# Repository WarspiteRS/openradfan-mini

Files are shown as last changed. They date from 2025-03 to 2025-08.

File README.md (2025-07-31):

# OpenRadFan
An ESPHome-driven smart controller for 12V PWM fans.

Classical radiators (K2/K3) typically require relatively high flow temperatures to heat up a room. Using forced convection can significally enhance their efficiency, especially at low flow temperatures. While there are a number of commercial solutions available, these did not need my needs. They are either too loud while running or switching on/off using a relays, don't properly switch at low flow temperatures, are too expensive or simply not powerful enough. Hence, I set out to build my own solution using standard 120/140mm PWM-capable PC fans. High-end fans run at low speeds (<500 RPM) are essentially inaudible and provide a definite boost to the room temperature. Being able to smartly control the fan speed and integrate them into Home Assistant - while not a must - is definitely very nice to have if you want to control fan speed based on time of day, current room temperature or room occupancy. The fans can even be used as a kind of thermostat to modulate room temperature without restricting flow to the radiators, which is especially crucial when using a heat pump that perform best with an open loop circulation and no TRVs.

Using these devices throughout our house, we can run out heat pump at flow temperatures typically reserved for good underfloor heating setups (Vaillant heat curve at 0.25 - 30°C flow temperature at 0°C, 35°C flow temperature at -10°C).

<p align="center">
  
</p>

## Features
### Hardware
- M5Stack Atom Lite / Atom Lite S3 pluggable µC with usable Grove port for arbitrary I2C device support
- 8 fan connectors in 2x4 rows *[OpenRadFan-mini only has 2 fan connectors in 2x1 rows]*
- Each row can be individually PWM controlled (this is not enabled by default)
- RPM measurement for the first fan in each row *[OpenRadFan-mini only has one fan in each row]*
- Global on/off switch for fans that don't support zero output at zero PWM
- Plug-in connector for two DS18B20-compatible temperature sensors *[OpenRadFan-mini only has one temperature sensor]*
- Power supply: 12V barrel jack (2.1/2.5 mm), center positive
- Reverse voltage & transient overvoltage protection, 2.5 A resettable fuse
### Software
- Fully ESPHome compatible
- Controllable via Home Assistant or through any browser via stand-alone webserver
- Automatic fan curve driven speed control
- Setup & Connection to local WiFi via improv WiFi Hotspot on first boot

## Set-up instructions
**Don't connect to USB when the Atom lite is plugged into the PCB - there is no mechanism to block voltages between the included buck converter and the computer.**
1. Compile & flash ESPHome firmware on the Atom Lite using USB. Skip this step if you have a pre-flashed controller. The ESPHome directory on GitHub contains the yaml as well as factory & ota images so you can directly flash this without a local ESPHome compiler set up.
2. Connect DS18B20 to the push-in terminal block. The wire designations are marked on the PCB and are (from left to right): +3.3V, Data, GND. It's easiest to insert them all at the same time. Hold the wires in one hand in the correct order and insert them into the terminal. Then push all orange levers down at the same time and push the wires down as far as possible. The levers should almost return to the initial position and not be stuck halfway down. If you want to use more than one sensor, you need to manually edit the ESPHome yaml and include the individual IDs of the DS18B20s.
<p align="center">
  
</p>
4. Plug in the Atom Lite controller module and fans.
5. Lastly, plug in the barrel plug to power the device
6. On first boot, the device will present a hotspot named "openradfan-xxxxxx", with xxxxxx being the last characters of the Atom Lite's MAC address. You can connect to it in order to enter your WiFi credentials. The passwort for the hotspot is "OpenRadFan". If you get a warning that the hotspot does not provide an internet connection, click "Yes" when asked to connect anyways. Then, point your browser to http://192.168.4.1 to open the config page. Tap/click on your home WiFi and enter the password. Note down the hostname shown after "Wifi Networks:" (here "openradfan-f9465c"), this is also the hostname you can use to connect to the web interface after it has connected to your Wifi via http://openradfan-xxxxxx. It might be required to power cycle if you don't see the device appearing in your network.
<p align="center">
  
  
  
</p>
8. Home Assistant should automatically detect the device under Settings --> Devices & Services

<p align="center">
  
</p>
9. You can adopt it in your local ESPHome environment. The full yaml code will be fethed from GitHub when you do so, so you can adapt the config if needed.
10. The web interface gives you full control over all aspects of the device. Over-the-air (OTA) updates can also be uploaded and flashed to the device.
<p align="center">
  
</p>

## Fan curve control
You can set 5 temperature points and associated fan speeds to build a temperature-dependent fan speed response. The speed between the points is interpolated linearly. The temperatures have to increase from 1 to 5; this is also enforced by internal logic. Temperatures above/below the highest/lowest setpoint keep the speed of this setpoint. Set "Auto Fan Curve Control" to on in order to use this feature.

In the below example, the fans are off below 20°C, increase between 0 and 29% speed in the range between 20 and 21°C, then increase up to 100% at 25°C. Above that, speed decreases to 28% at 30°C and the fans are off again at 35°C.

When fan speed is set to zero, the internal high-level switch also cuts all power to the fans. Some fans (e.g. Arctic PXX PWM) turn off with a zero PWM signal and wouldn't need this functionality, however many other fans cannot be turned off via PWM alone.
<p align="center">
  
</p>

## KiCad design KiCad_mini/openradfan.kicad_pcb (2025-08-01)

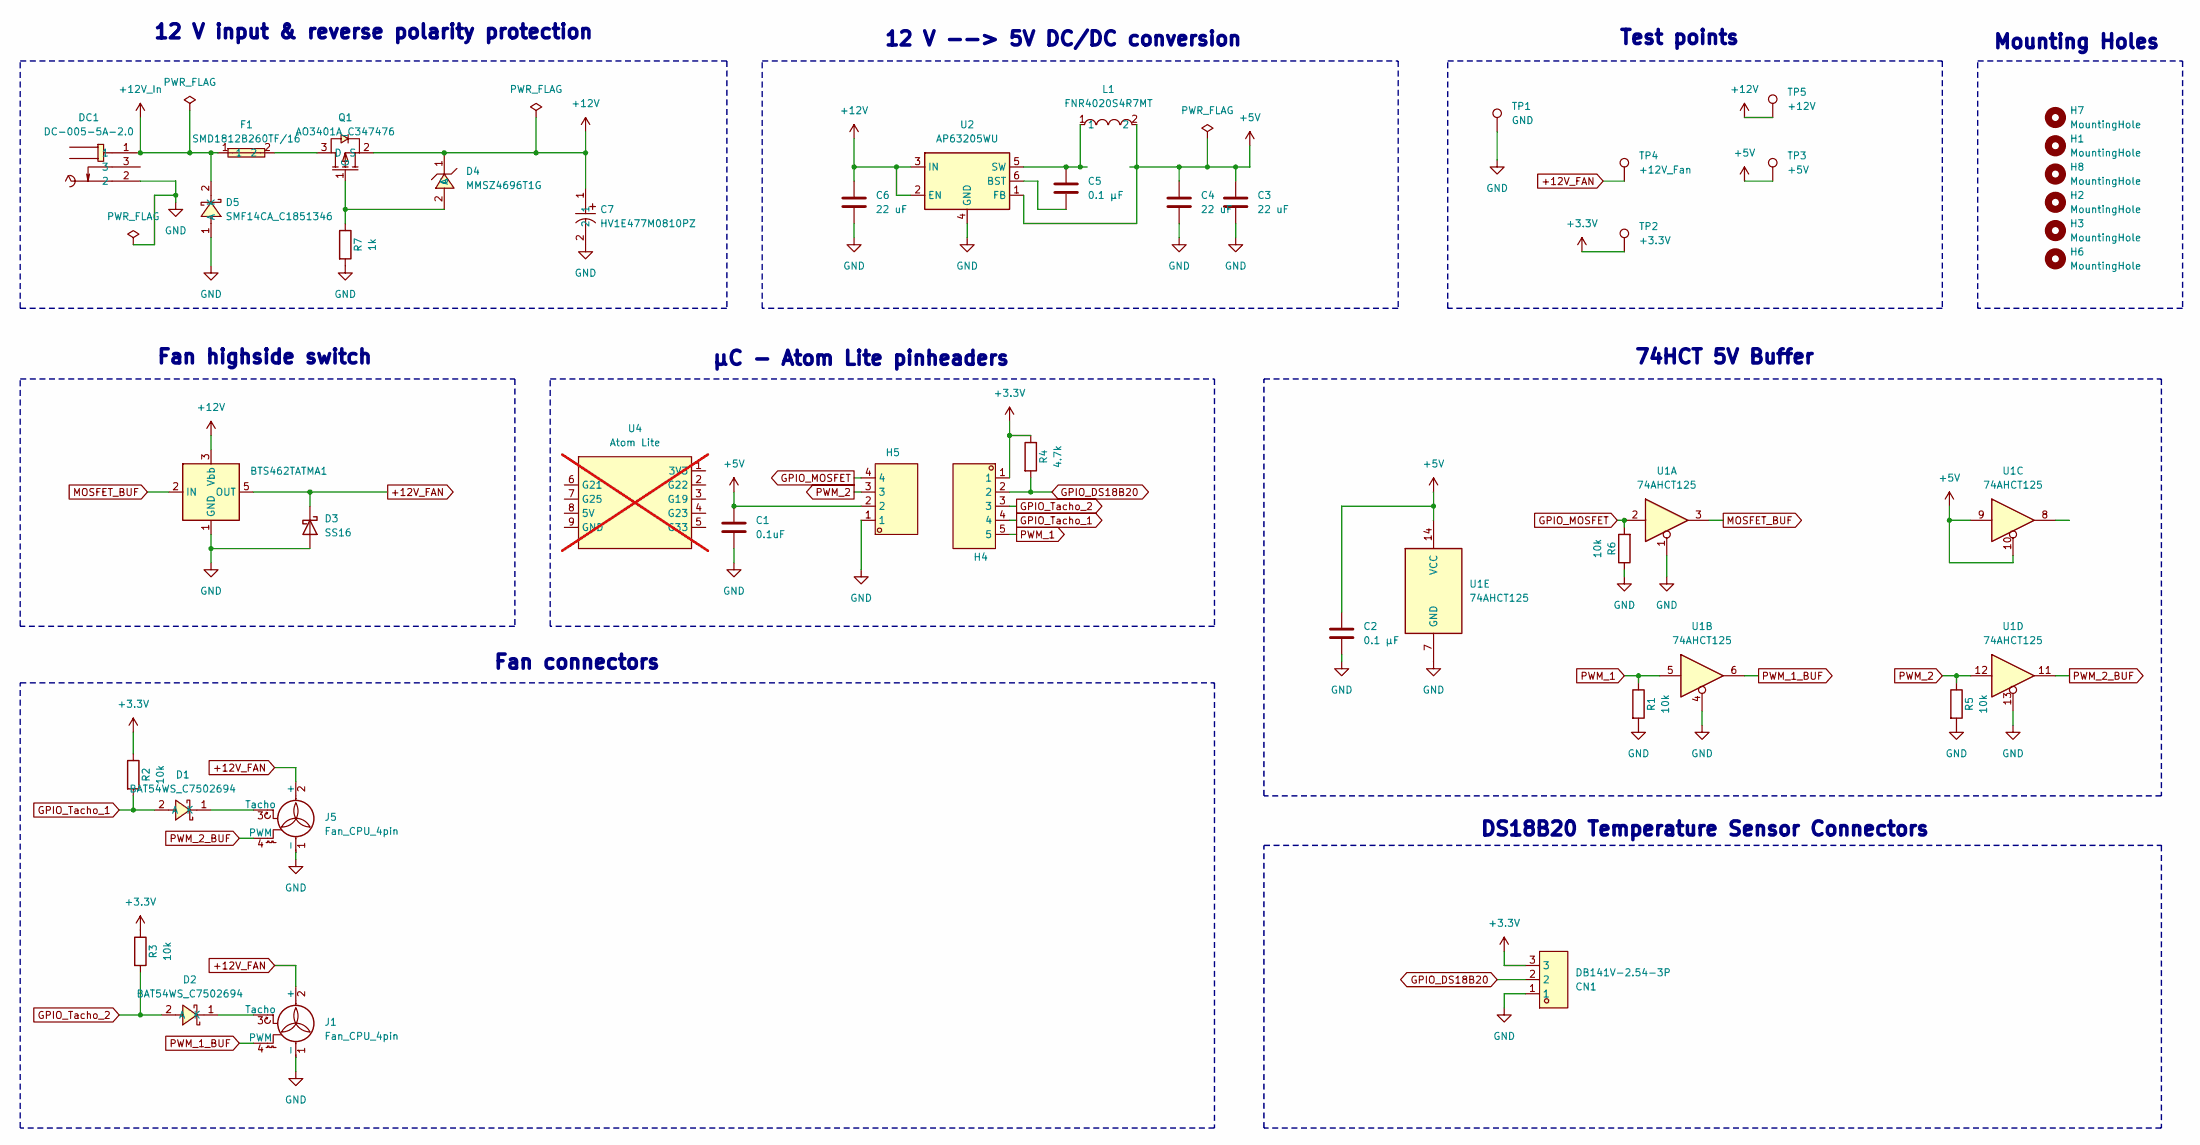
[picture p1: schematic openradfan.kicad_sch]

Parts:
C1: 0.1uF; C_0805_2012Metric_Pad1.18x1.45mm_HandSolder; LCSC Part # C28233
C2: 0.1 µF; C_0805_2012Metric_Pad1.18x1.45mm_HandSolder; LCSC Part # C28233
C3, C4, C6: 22 uF; C_1210_3225Metric; LCSC Part # C309062
C5: 0.1 µF; C_0402_1005Metric; LCSC Part # C1525
C7: HV1E477M0810PZ; CAP-SMD_BD8.0-L8.3-W8.3-LS9.3-FD-2; LCSC Part C5246546
CN1: DB141V-2.54-3P; CONN-TH_3P-P2.54_DIBO_DB141V-2.54-3P; LCSC Part C2898745
D1, D2: BAT54WS_C7502694; SOD-323_L1.7-W1.3-LS2.6-RD-1; LCSC Part C7502694
D3: SS16; D_SMA; LCSC Part # C2481
D4: MMSZ4696T1G; SOD-123_L2.7-W1.6-LS3.7-RD-1; LCSC Part C462868
D5: SMF14CA_C1851346; SOD-123_L2.8-W1.8-LS3.7-BI; LCSC Part C41411783
DC1: DC-005-5A-2.0; DC-IN-TH_DC-005-5A-2.0; LCSC Part C381116
F1: SMD1812B260TF/16; F1812; LCSC Part C269148
H1, H2, H7, H8: MountingHole; MountingHole_3.2mm_M3_DIN965
H3, H6: MountingHole; MountingHole_2.2mm_M2_DIN965
H4: 210S-1*5P L=11.6MMGold-plated black; HDR-TH_5P-P2.54-V-M; LCSC Part C124379
H5: Header-Male-2.54_1x4; HDR-TH_4P-P2.54-V-M; LCSC Part C124378
J1, J5: Fan_CPU_4pin; FanPinHeader_1x04_P2.54mm_Vertical; MPN 0470531000; LCSC Part # C240840
L1: FNR4020S4R7MT; IND-SMD_L4.0-W4.0_FNR40XXS; LCSC Part C167828
Q1: AO3401A_C347476; SOT-23_L2.9-W1.3-P1.90-LS2.4-BR; LCSC Part C347476
R1, R2, R3, R5, R6: 10k; R_0805_2012Metric_Pad1.20x1.40mm_HandSolder; LCSC Part # C17414
R4: 4.7k; R_0805_2012Metric_Pad1.20x1.40mm_HandSolder; LCSC Part # C17673
R7: 1k; R_0603_1608Metric; LCSC Part # C21190
TP1: GND; TestPoint_Keystone_5000-5004_Miniature
TP2: +3.3V; TestPoint_Keystone_5000-5004_Miniature
TP3: +5V; TestPoint_Keystone_5000-5004_Miniature
TP4: +12V_Fan; TestPoint_Keystone_5000-5004_Miniature
TP5: +12V; TestPoint_Keystone_5000-5004_Miniature
U1: 74AHCT125; SOIC-14_3.9x8.7mm_P1.27mm; MPN SN74AHCT125N; LCSC Part # C352957
U2: AP63205WU; TSOT-23-6; LCSC Part # C2071056
U3: BTS462TATMA1; TO-252-4; LCSC Part # C3232325
U4: Atom Lite; not fitted

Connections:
+3.3V: CN1.3, H4.1, R2.1, R3.1, R4.1, TP2.1
+5V: C1.1, C2.1, C3.1, C4.1, H5.2, L1.2, TP3.1, U1.9, U1.10, U1.14 (VCC), U2.1 (FB)
+12V: C6.1, C7.1, D4.1 (C), Q1.2 (S), TP5.1, U2.2 (EN), U2.3 (IN), U3.3 (Vbb)
+12V_FAN: D3.1 (K), J1.2 (+), J5.2 (+), TP4.1, U3.5 (OUT)
+12V_In: D5.2 (K), DC1.1, F1.1
GND: C1.2, C2.2, C3.2, C4.2, C6.2, C7.2, CN1.1, D3.2 (A), D5.1 (A), DC1.2, H5.1, J1.1 (-), J5.1 (-), R1.2, R5.2, R6.1, R7.2, TP1.1, U1.1, U1.4, U1.7 (GND), U1.13, U2.4 (GND), U3.1 (GND)
GPIO_DS18B20: CN1.2, H4.2, R4.2
GPIO_MOSFET: H5.4, R6.2, U1.2
GPIO_Tacho_1: D1.2 (A), H4.4, R2.2
GPIO_Tacho_2: D2.2 (A), H4.3, R3.2
MOSFET_BUF: U1.3, U3.2 (IN)
unnamed: D1.1 (K), J5.3 (Tacho)
unnamed: D2.1 (K), J1.3 (Tacho)
unnamed: D4.2 (A), Q1.1 (G), R7.1
unnamed: F1.2, Q1.3 (D)
unnamed: C5.2, U2.6 (BST)
unnamed: C5.1, L1.1, U2.5 (SW)
PWM_1: H4.5, R1.1, U1.5
PWM_1_BUF: J1.4 (PWM), U1.6
PWM_2: H5.3, R5.1, U1.12
PWM_2_BUF: J5.4 (PWM), U1.11

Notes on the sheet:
12 V input & reverse polarity protection
12 V --> 5V DC/DC conversion
µC - Atom Lite pinheaders
Fan connectors
Mounting Holes
74HCT 5V Buffer
Test points
Fan highside switch
DS18B20 Temperature Sensor Connectors

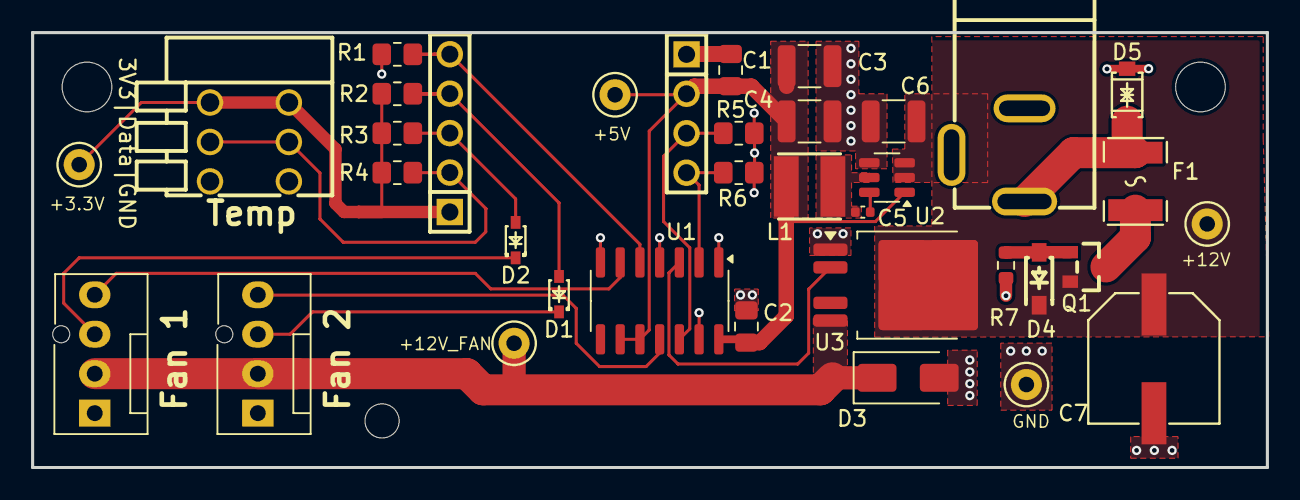
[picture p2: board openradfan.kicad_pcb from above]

Board: 2 copper layers, 79.5 x 28.0 mm, 39 parts (0 on the bottom side), 21 nets.

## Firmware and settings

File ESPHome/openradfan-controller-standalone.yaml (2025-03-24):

substitutions:
  device_name: "openradfan"
  device_name_friendly: "OpenRadFan"
  time_zone: "Europe/London"
  control_temp_min: "20"
  control_temp_max: "35"
  
# Add the global variable declaration
globals:
  - id: enforce_temp_constraints_ptr
    type: std::function<void(float, int)>
  - id: calculate_curve_speed_ptr
    type: std::function<void(float)>

esphome:
  name: "${device_name}-standalone"
  friendly_name: "${device_name_friendly}"
  name_add_mac_suffix: true
  project:
    name: esphome.openradfan-controller
    version: "1.2"
  on_boot:
    then:
      # These functions calculate the current Fan Curve Speed and also enforce constraints on the inputs,
      # i.e. increasing temperature points
      - lambda: |-
          // Helper function to enforce temperature constraints
          auto enforce_temp_constraints = [](float new_value, int index) -> void {
            std::vector<template_::TemplateNumber*> temps;
            temps.push_back(id(curve_temp_1));
            temps.push_back(id(curve_temp_2));
            temps.push_back(id(curve_temp_3));
            temps.push_back(id(curve_temp_4));
            temps.push_back(id(curve_temp_5));
            
            // Set the new value for the changed temperature
            temps[index]->publish_state(new_value);
            
            // Propagate up if necessary (ensure following temps are not lower)
            for (int i = index + 1; i < temps.size(); i++) {
              if (temps[i]->state < new_value) {
                temps[i]->publish_state(new_value);
              }
            }
            
            // Propagate down if necessary (ensure preceding temps are not higher)
            for (int i = index - 1; i >= 0; i--) {
              if (temps[i]->state > new_value) {
                temps[i]->publish_state(new_value);
              }
            }
          };
          
          // Store the function globally so we can access it in number components
          id(enforce_temp_constraints_ptr) = enforce_temp_constraints;

          // Helper function to calculate current curve speed
          auto calculate_curve_speed = [](float current_temp) -> void {
            std::vector<template_::TemplateNumber*> temps;
            temps.push_back(id(curve_temp_1));
            temps.push_back(id(curve_temp_2));
            temps.push_back(id(curve_temp_3));
            temps.push_back(id(curve_temp_4));
            temps.push_back(id(curve_temp_5));
            
            std::vector<template_::TemplateNumber*> speeds;
            speeds.push_back(id(curve_speed_1));
            speeds.push_back(id(curve_speed_2));
            speeds.push_back(id(curve_speed_3));
            speeds.push_back(id(curve_speed_4));
            speeds.push_back(id(curve_speed_5));
            
            // Find the temperature segment
            for (int i = 0; i < temps.size() - 1; i++) {
              float temp1 = temps[i]->state;
              float temp2 = temps[i + 1]->state;
              
              if (current_temp >= temp1 && current_temp <= temp2) {
                // Linear interpolation between speed points
                float speed1 = speeds[i]->state;
                float speed2 = speeds[i + 1]->state;
                float t = (current_temp - temp1) / (temp2 - temp1);
                float current_speed = speed1 + t * (speed2 - speed1);
                
                id(current_curve_speed)->publish_state(current_speed);
                return;
              }
            }
            
            // Handle temperature outside the curve
            if (current_temp < temps[0]->state) {
              id(current_curve_speed)->publish_state(speeds[0]->state);
            } else {
              id(current_curve_speed)->publish_state(speeds[speeds.size()-1]->state);
            }
          };
          
          // Store the function globally
          id(calculate_curve_speed_ptr) = calculate_curve_speed;

# ESP32 platform to use
esp32:
  board: m5stack-atom
  framework:
    type: esp-idf

# API is a requirement of the dashboard import.
# api:

# This should point to the public location of this yaml file.
# dashboard_import:
#   package_import_url: github://andrekuehne/openradfan/ESPHome/openradfan-controller.yaml@main
#   import_full_config: true

# To be able to get logs from the device via serial and api.
logger:
  level: INFO

# OTA is required for Over-the-Air updating
ota:
  - platform: esphome

wifi:
  # Set up a wifi access point
  ap:
    password: "OpenRadFan"

# In combination with the `ap` this allows the user
# to provision wifi credentials to the device.
captive_portal:

# Sets up Bluetooth LE (Only on ESP32) to allow the user
# to provision wifi credentials to the device.
esp32_improv:
  authorizer: none

# Web server to allow control also without Home Assistant
web_server:
  version: 3
  port: 80
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

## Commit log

2025-02-11 Create openradfan-controller.yaml
    Added initial ESPHome YAML code
    [openradfan-controller.yaml]
2025-02-11 Added package import URL to adopt device
    [openradfan-controller.yaml]
2025-02-11 Removed room name
    [openradfan-controller.yaml]
2025-02-11 Fixed accidental yaml typos
    [openradfan-controller.yaml]
2025-02-13 Include I2C, commented out SCD4x code for reference
    [openradfan-controller.yaml]
2025-02-13 Included safety components
    Include reverse voltage protection, transient overvoltage protection & a resettable fuse
    [openradfan.kicad_pcb, openradfan.kicad_sch]
2025-03-03 Create m5stack-atom-lite.h to fix unwanted button triggers
2025-03-15 Simplify debugging
    - Store values of power on etc.
    - Uptime sensor
    - debugging active
    - Sensor for last reset reason
    [openradfan-controller.yaml]
2025-03-15 Add heap stats to debug sensors
    [openradfan-controller.yaml]
2025-03-15 Fixed debug sensor
    [openradfan-controller.yaml]
2025-03-16 Switched to ESP-IDF framework
    - Fixed save to flash for temperature curve values
    - Reduced sampling rate of DS18B20
    - Turned off I2C by default
    ESP-IDF led to massively more free RAM. Controller appears much more stable.
    [openradfan-controller.yaml]
2025-03-16 Switched web_server to version 3
    [openradfan-controller.yaml]
2025-03-24 Added automatic standalone yaml creation
    [openradfan-controller-standalone.yaml]
2025-03-24 Added automatic api and standalone build scripts
    [openradfan-controller-standalone.yaml, openradfan-controller.yaml]
2025-07-31 Prototype fixes
    [openradfan.kicad_pcb]
2025-07-31 Proto rearrangement
    [openradfan.kicad_pcb]
